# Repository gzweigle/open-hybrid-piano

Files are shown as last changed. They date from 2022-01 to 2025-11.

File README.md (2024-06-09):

# Hybrid MIDI Digital Piano

Also known as **stem piano**

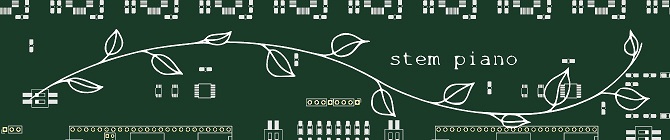
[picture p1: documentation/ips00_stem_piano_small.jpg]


## How to Build A Hybrid Piano
Go straight to the [pianos/](pianos/) directory!

But first, please read the [WARNINGS](WARNINGS.md) and [HELP](HELP.md) files that are located in this root directory.

See the [STATUS](STATUS.md) file for status of the project and repository.

If you would like to contribute hardware, software, mechanical, or firmware to the project, see the [CONTRIBUTING](CONTRIBUTING.md) file.

**If you build a piano, please share about it in the Show & Tell Discussions of this repository.**

## Overview

A hybrid piano combines the physical action of an acoustic piano with MIDI, sound generation, and other features of a digital keyboard. Some piano manufacturers sell hybrid pianos.

This project ("*stem piano*") is an open-source hybrid digital piano.

The qualifier digital is important. It means that signals are sampled with an analog-to-digital converter (ADC) and then all processing is with a microprocessor. Therefore, once the hardware is installed all algorithms, improvements, and new features are with software or firmware.

The repository includes schematics, printed circuit board layouts, firmware source files for the real-time processing, optional software source files for Ethernet connected features, and lists of required hardware components.

A physical piano action, or other instrument, is required. The electronics and code (*stem piano*) will work with a grand or upright piano action. Mechanical suggestions are included but not detailed mechanical instructions.

The platform and code could also adapt to building a range of other unique and innovative musical instruments.

## Directory Organization

The components required to build a piano are located in the [firmware/](firmware/), [hardware/](hardware/), [mechanical/](mechanical/) and [software/](software/) directories. In each directory is a *research* subdirectory and a *releases* subdirectory.

Each *research* subdirectory contains code and hardware for work in progress. It could have major bugs. It could be incomplete.

Each *releases* subdirectory contains code and hardware ready for use. The material in *releases* could partially duplicate material in one or more *research* subdirectories. However, the requirement is that anything in *releases* is well-tested, complete, and ready-to-use.

More details on each directory:

#### [design/](design/)

Designs and engineering analysis. To keep the repository small, associated data may be located in the separate Piano-Data repository.

#### [documentation/](documentation/)

High level documentation.

Includes [documentation/video_documentation.md](documentation/video_documentation.md) for historical, how-to, and other documentation in video form.

#### [pianos/](pianos/)

Building a complete piano requires firmware, hardware, mechanical, and sometimes software. The *pianos/* directory provides information on everything needed to build a specific version of a musical instrument.

Best place to start for learning the firmware, software, mechanical, and hardware.

#### [firmware/](firmware/)

Real-time code running on custom hardware from *hardware/* directory.

#### [hardware/](hardware/)

All printed circuit boards and related parts and design. A separate open-source license for the hardware is in this directory and applies to all hardware.

#### [mechanical/](mechanical/)

Anything to physically build a piano. A separate open-source license for mechanical is in this directory and applies to anything mechanical.

#### [software/](software/)

Code running on a standard computer or Raspberry Pi connected to the piano over Ethernet or MIDI.

## Repositories

#### (1) Original

This "DIY" repository. Organized per above.

#### (2) Stem Piano

https://github.com/stem-piano

Experimenting with a GitHub organization. The documentation and links for building individual pianos is here. Links are back to this original "DIY" repository.

May or may not migrate all files in the future. To be decided in the future.

## Related Projects:

Work was inspired, in part, by https://github.com/ekumanov/cybrid

See also:

* https://github.com/jkominek/piano-conversion/
* https://github.com/davidedelvento/Mybrid
* https://www.youtube.com/watch?v=nRBsudMpwwc
* https://www.youtube.com/watch?v=-kpf0OSJxkE
* https://www.youtube.com/watch?v=b-PRGymqECM

## "stem piano" because?

* science technology engineering math
* like a plant stem, everything here is one component of the overall instrument
* like a note stem, everything here is one component of...
* 12 leaves on the logo, matches 12 piano notes
* logo looks like a sine wave
* sounds cool
* does not sound cool

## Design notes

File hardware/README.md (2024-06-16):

# Stem Piano Hardware
See [kicad_general.md](./kicad_general.md) in this directory for information on the libraries.

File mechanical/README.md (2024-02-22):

# Mechanical Design

## Overview

The design is very flexible:
* Will work on grand and upright pianos.
* Will work with the action separate from the piano or as a silent system in a full piano.
* Will work with a digital keyboard, using sensors on the digital keys.
* Can use as part of innovative new musical instruments.

In the *documentation/* directory under the root directory is a file called video_documentation.md.  Please see for installation examples.

## Grand Piano - Separate Action Examples

### Stem Piano Model G

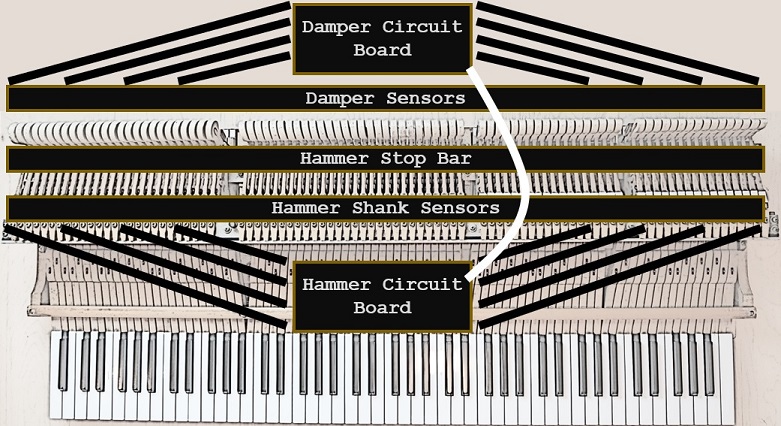
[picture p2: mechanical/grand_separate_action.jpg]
grand_separate_example


#### Damper Sensors

An aluminum L-shaped bar is placed across the back of the action. The damper sensors are mounted on this bar.

Connect the damper sensors to the circuit board that is processing the damper sensor output signals.

#### Hammer Stop Bar

Connect a strong steel bar that is anchored to something solid. Adjust height so that the hammer shanks hit this stop at the position where in a full piano the hammer would have hit a string.

#### Hammer Shank Sensors

An aluminum L-shaped bar is placed across the top-front of the action. The hammer sensors are mounted on this bar.

Connect the hammer sensors to the circuit board that is processing the hammer sensor output signals.

When two or more keys are pressed with identical force, the volume should be identical.  This note-to-note volume consistency is directly related to consistency of the sensor-to-shank physical distance between keys.

## Grand Piano - Silent System Examples

## Upright Piano - Separate Action Examples

## Upright Piano - Silent System Examples

## Innovative Instruments Examples

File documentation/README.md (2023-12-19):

# DIY Hybrid Digital Grand Piano - High Level Documentation

Three versions of the piano are in development. More are likely in the future. Further details, design, code, and hardware is in the root level *firmware*, *hardware*, *mechanical*, and *software* directories.

If a piano based on one of these architectures is stable enough for release, then information on all components required to build the piano is in the root level *pianos* directory.

## Performance Architecture
The original architecture.

Designed for maximum performance, without constraining cost or practicality. Sampling is fully parallel and in range 8Ksps to 32Ksps.

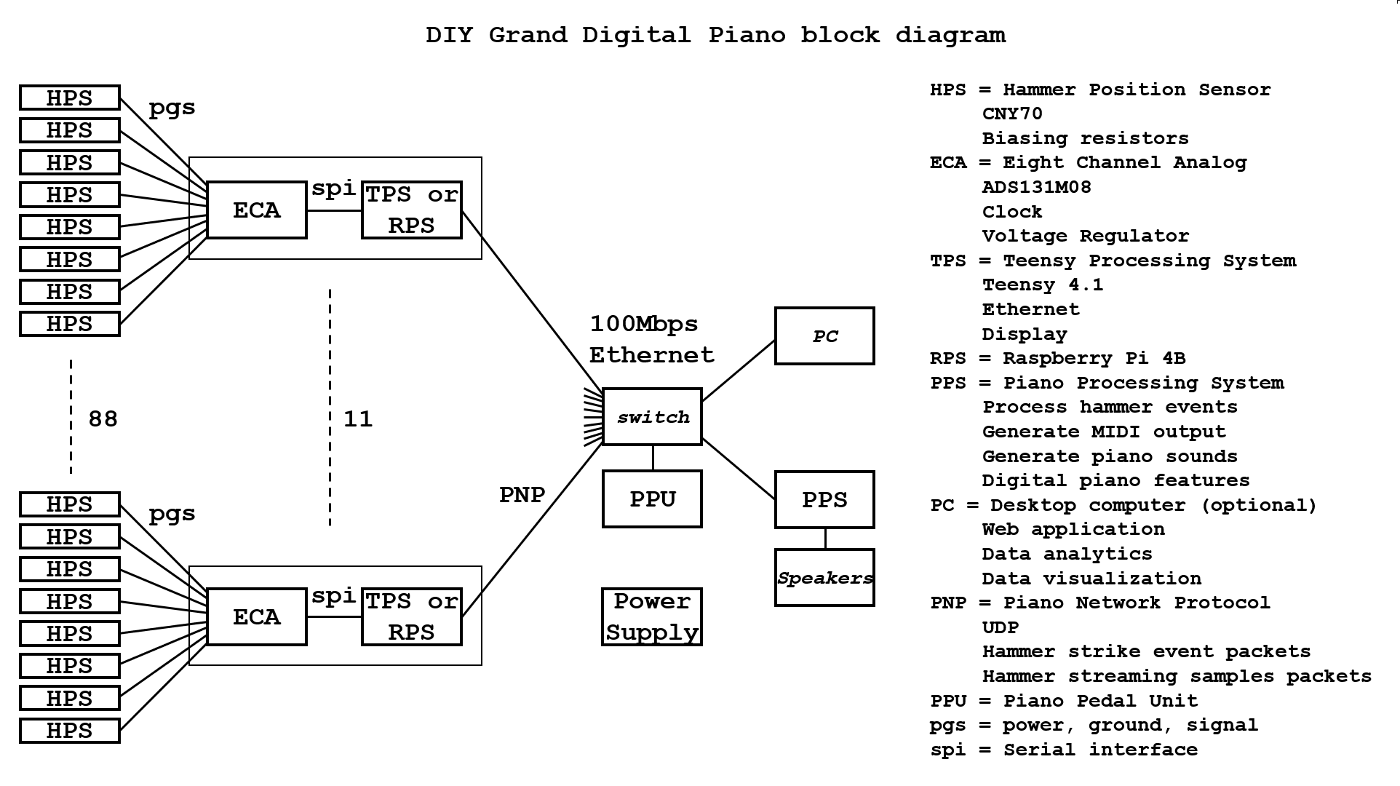
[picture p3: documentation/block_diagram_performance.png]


## Single Board Architecture 0.0
First single board architecture. An attempt to simplify and lower the cost. Sampling is fully parallel and in range 2Ksps to 8Ksps. Results show this architecture gives up performance without much benefit to simplicity or cost.

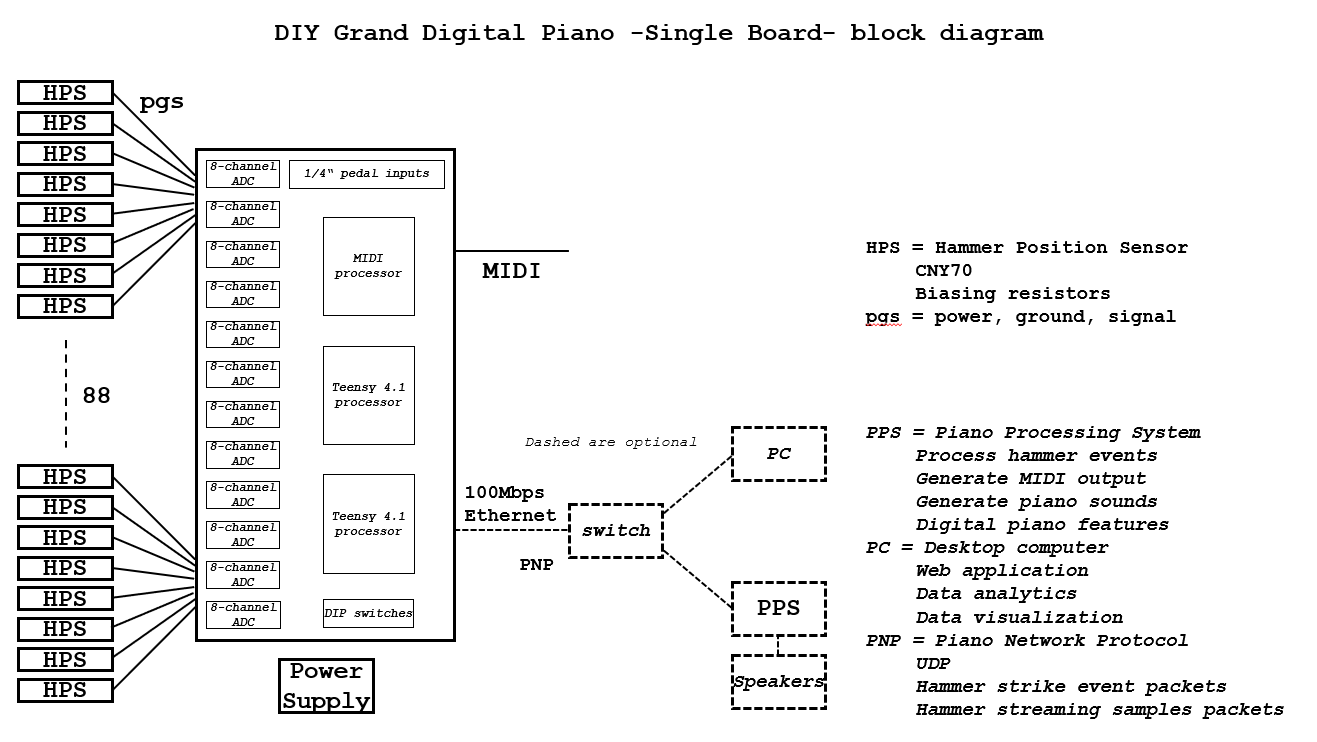
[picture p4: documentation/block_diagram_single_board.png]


## Single Board Architecture 2.0
Calling it "1.0" is too boring. Straight to 2.0!

Initially, this architecture was developed for damper processing. It was called the Damper Position Processor. Dampers do not need high-speed sampling and so, for dampers, sampling was fully sequential (a single ADC, multiplexed).

However, after testing and thinking more about it, I combined parallel plus sequential sampling into a design that scales from damper to hammer speeds. Preliminary analysis shows that the upper sampling limit could be close to the original performance architecture.

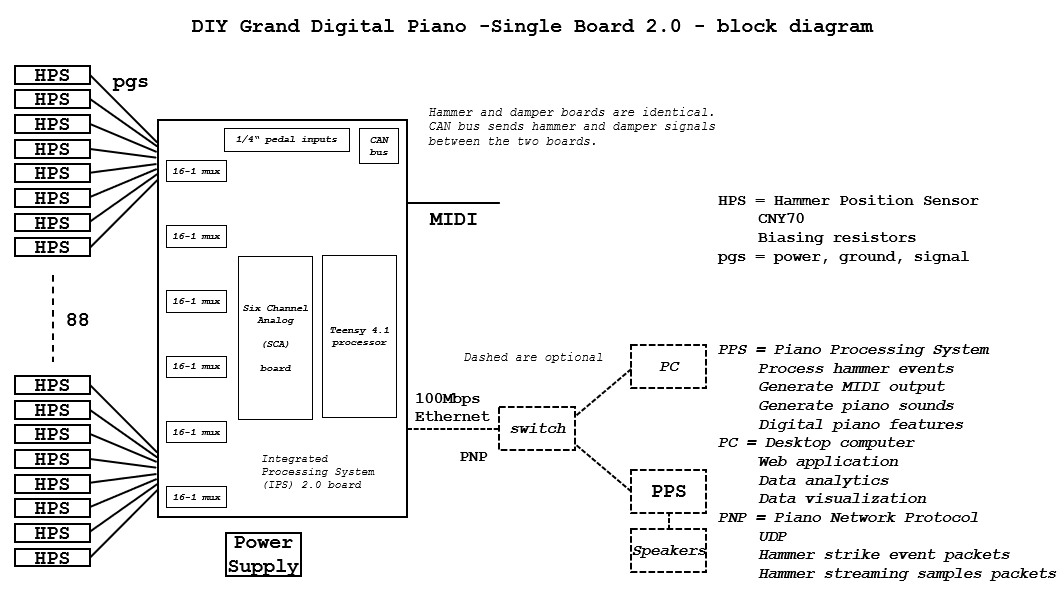
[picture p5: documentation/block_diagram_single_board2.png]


## Components Include:

Processors:
* Teensy 4.1 ARM Processor - https://www.pjrc.com/store/teensy41.html
* Raspberry Pi - https://www.raspberrypi.com/

Digital:
* Teensy to ADC interface logic ICs

Displays:
* Adafruit 2.8 inch TFT display - https://www.adafruit.com/product/1770

Analog:
* Texas Instruments ADS131M08 - https://www.ti.com/product/ADS131M08
* Texas Instruments ADS8861 - https://www.ti.com/product/ADS8861
* Texas Instruments ADS8860 - https://www.ti.com/product/ADS8860
* Texas Instruments ADCS7476 - https://www.ti.com/product/ADCS7476
* LTC6930 Precision Oscillator - https://www.analog.com/en/products/ltc6930.html
* 300mA - 500mA Low Dropout Linear Regulator
* 16:1, 8:1, and similar analog multiplexers
* CNY70 Sensor - https://www.vishay.com/en/product/83751/

Languages:
* Python - https://www.python.org/
* Matlab - https://www.mathworks.com/products/matlab.html
* C++

Printed Circuit Boards:
* OSH Park - https://oshpark.com/

## Video Documentation

Please see [YouTube Posts](video_documentation.md) for historical, how-to, and other documentation in video form.

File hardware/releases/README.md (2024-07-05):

# Hardware Releases

All released hardware is located in this directory.

See [../kicad_general.md](../kicad_general.md) for more information on KiCad files.

## Manufacturing

### Gerber Files

To manufacture a circuit board, send the files in a *_gerber/ folder to a PCB manufacturer. Board fabrication and test is always with the *_gerber/ folder files.

If the circuit board directory does not include a *_gerber/ folder, this means the boards have not been fully fabricated and tested. In this case, use the KiCad project. Once tested, add a *_gerber/ folder and files.

### KiCad Project Files

Boards for Gerber files were fabricated and tested.

Each directory of KiCad project files end with a "KiCad files" _v* version number. The KiCad libraries directories in this repository also end with the same "KiCad Files" _v* version number. Use the KiCad libraries directory with the same "KiCad files" _v* version number as the KiCad project files directories.

The "KiCad files" _v* version number system is a different numbering system than the KiCad program version and is different than the circuit board version. A unique "KiCad files" _v* version number for the KiCad directories allows flexible updates with anything related to KiCad changes.

### Components

Each bill of materials file ends with a number. This number allows different component variants for the same board. Piano building instructions will specify the bill of materials variant.

For any discrepancy between schematic and bill of materials, use the bill of materials. This includes part values as well as whether a through-hole component is placed on front or back of a circuit board.

## Numbering Systems Summary

* Circuit board version. Each circuit board version is in its own unique subdirectory.
* Bill of materials. The number on each bill of materials is for a board variant. Instructions for building each piano will specify the correct bill of materials variant.
* KiCad files _v* version number. Use this number to match KiCad files with the symbol and footprint library files in this repository.
* KiCad program version. If a circuit board directory includes multiple KiCad program versions, the circuit boards may have a silkscreen label indicating the KiCad program version used for fabrication.

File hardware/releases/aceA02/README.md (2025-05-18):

# Analog Condition Equalize (ACE) "A" - Version 0.2

Identical to ACE A 0.1 with the following changes:
* Add wire labels.
  * "+" = power
  * "-" = ground
  * "!" = signal
* Move connector labels closer to connectors.
* Space the resistors slightly further apart.
* Minor trace movement. No connectivity changes.

No functional changes.

See ACE A 0.0 for detailed description.

ACE A 0.0, 0.1, and 0.2 functionality and connectivity are identical.

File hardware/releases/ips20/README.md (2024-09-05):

# Integrated Processing System 2 (IPS2) specification

The mainboard for hammer or damper sensor connections and Teensy 4.1 processing.

## Features

### I/O
* The board supports 96 sensor inputs.
  * Either:
    * Analog interfaces to 88 hammer sensor boards, or
    * Analog interfaces to 88 damper sensor boards.
  * 3 pedal inputs: 1/4 inch.
  * With less pedal inputs, it is also possible to use extra inputs for more than 88 piano keys.
  * With less piano key inputs, it is also possible to have more pedal inputs.
* MIDI output.
* Ethernet interface (optional).
* +5 volt, 1.75 amp power input. Current is when using with 88 HPS 0.4 or HPS 0.8 sensors. Current input could be different with alternate sensor.
* CAN bus.

### Capabilities
* Process hammer samples and generate MIDI outputs.
* Process damper samples and send to hammer processing board.
* Process pedal samples and generate MIDI outputs.
* Dual in-line package switches for configuration.
* Optional advanced monitoring, setup, and analytics over Ethernet and web brower.
* Optional hammer and pedal data over Ethernet using the piano network protocol (PNP).
* Optional TFT display for setup.

### Components
* Selected for availability.
* Relatively large pitch, relatively easy to solder parts.
* Requires a Six Channel Analog (SCA) card.
* The parts list(s) includes an index number in the file name to support differences depending on application. Files:
  * [./ips20_bill_of_materials_0.txt](./ips20_bill_of_materials_0.txt)

## Form
* 8.5 inches by 4.0 inches.
* Single board.

## Top Level PCB Description

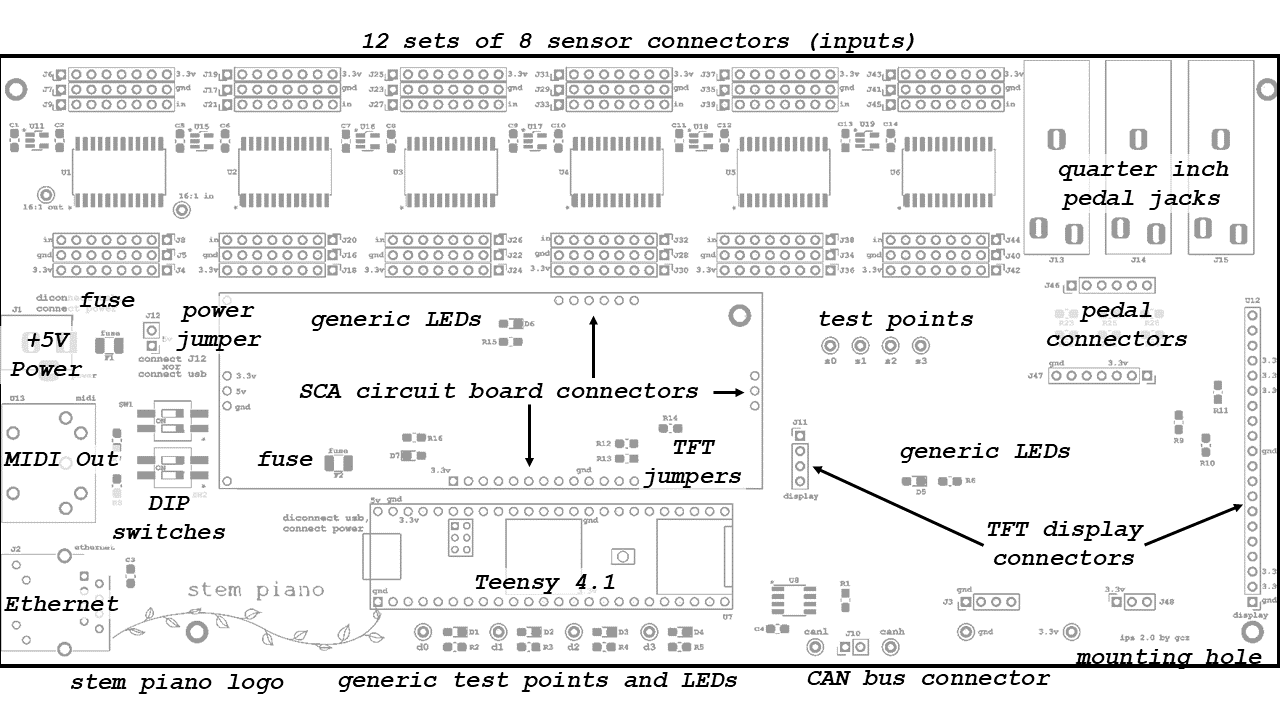
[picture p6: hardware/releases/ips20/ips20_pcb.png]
ips20_pcb


### Sensor connectors
0.1 inch spaced connectors for connecting wires to the Hammer Position Sensor (HPS) boards. Does not require HPS boards. Can connect to any sensor system that meets input signal requirements.

### Quarter inch pedal jacks
For connecting pedals.

See discussion in issue: https://github.com/gzweigle/DIY-Grand-Digital-Piano/issues/74

### Pedal connectors
0.1 inch spaced connectors J46. Connect to six of the sensor connectors. See instructions in the *pianos/* directory for this board.

### +5V power

* Cut the 5V pad on Teensy 4.1 per instructions at PJRC website before installing the Teensy processor. https://www.pjrc.com/teensy/external_power.html

* See: https://github.com/stem-piano/stem-piano-top/blob/main/WARNINGS.md

### Fuse

Location for fuses. The +5V power and USB must must automatically protect from short circuits, overcurrent, thermal, and all other failure conditions

User to decide on PCB fuse design and strategy. See the bill of materials file(s) in this directory.

Here is a short video on the *stem piano* historical progress YouTube channel about removing and replacing a surface mount fuse. Also see other resources on the internet.
https://www.youtube.com/watch?v=TsNTWSIT84I

### Power jumper (J12)
Install only after 5V pad on Teensy 4.1 is cut per instructions at PJRC website.

https://www.pjrc.com/teensy/external_power.html

### MIDI Out
Five-pin MIDI output connection. The board does not have a MIDI input.

### Ethernet
Ethernet connection.

### DIP switches
For simple configuration settings. Programmable with the Teensy firmware. See code for functionality.

### SCA circuit board connectors
The analog-to-digital conversion (ADC) subsystem is on a separate, removable, card that connects to the IPS printed circuit board. This simplifies and reduces the cost of testing an ADC and enables experimenting with different hammer or damper ADC resolution and sampling rates. Also, ADC parts can often be in packages that are difficult to solder. A separate circuit board lowers the cost and impact of soldering mistakes.

Headers J3, J47, and J48 make it possible to increase the size of the SCA. This allows larger and more complex analog circuits. In this case, either do not use the TFT, or use longer connectors so the TFT is above the SCA.

### Generic test points and LEDs
Programmable test points and LEDs through the Teensy firmware.

### Teensy 4.1
What makes everything possible.

### TFT jumpers
Zero-ohm resistors R12, R13, and R14. Only needed if TFT display is connected.

### CAN bus connector
Connect two wires between hammer and damper circuit boards. If not using a damper circuit board then leave these disconnected. Connect each wire to the same location on the other board (left side of connection to left side, right side to right side).

### TFT display connectors
Connection for optional 2.8-inch display.

### stem piano logo
Yeah!!

## Power Supplies and Connections

[ips20_power.md](./ips20_power.md)

## Design
Location of timing analysis: [../../../design/data_acquisition/eca0X_ips2X/eca0X_ips2X_timing_design.md](../../../design/data_acquisition/eca0X_ips2X/eca0X_ips2X_timing_design.md).

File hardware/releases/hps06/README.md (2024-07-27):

# Hammer Position Sensor (HPS) Version 0.6

## Introduction

Originally, the HPS PCB was for hammers.  However, the sensor also works for dampers.  Not changing the name because many circuit boards have already been built.

This circuit board includes a trimming resistor. Unless needed for a specific use case, the circuit board with trimming resistor is not recommended.

In repository for historical reasons.

## Features

### I/O
* Power input.
* Analog output signal, with range set by resistors.
* Ground.

### Size
* 1.5 inches long.
* 0.4 inches wide.

### Capabilities
* CNY70 sensor.
* Trimming resistor to fine tune output voltage maximum value.
* All resistors are surface mount packages.

### Pin Order:
* Power
* Signal
* Ground

## Calibrating

Adjust the RV0 trimming resistor to get the output voltage in the correct range. A 1.0mm flathead screwdriver is required. Turn the screw slowly and gently. Information according to the datasheet [Bourns 3224 - 4mm SMD Trimpot Trimming Potentiometer, C1753 5/17/18]:
* Adjustment angle = 12 turns.
* Rotational cycling max = 200 cycles.

Based on testing, typical adjustment is no more than approximately 2 turns clockwise or counterclockwise. This results in a resistance range of approximately 75 to 125 ohms.

Turning the RV0 trimming screw clockwise decreases the resistance between pins 2 and 3 of the trimming resistor RV0 ==> this decreases the combined resistance R1 + RV0 ==> this increases the forward current of the CNY-70 emitter ==> this increases the output voltage.

Turning the RV0 trimming screw counterclockwise increases the resistance between pins 2 and 3 of the trimming resistor RV0 ==> this increases the combined resistance R1 + RV0 ==> this decreases the forward current of the CNY-70 emitter ==> this decreases the output voltage.

R2 sets the maximum output voltage. If the output voltage is too large, the analog-to-digital converter will clip. If the output voltage is smaller, it decreases the dynamic range. The piano will work with a lower dynamic range but may not work if the signal is clipping. Therefore, if the R2 value in bill of materials is unavailable, choose a smaller value.

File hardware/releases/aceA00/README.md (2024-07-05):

# Analog Condition Equalize (ACE) "A" - Version 0.0

## Introduction

The ace A is an interposer card between sensors and mainboard for analog signal translation.

Each ace A snaps onto the mainboard at 16 sensor connections at rear of mainboard.

Each interposer function is identified by a letter.

| Letter | Function |
|---|---|
| A | Resistor load (this README file)  |
| B | Transimpedance amplifier (future) |
| Z | Pass through (future) |

## Description

Each ace card connects 16 sensors to the mainboard. See the specific stem piano construction documentation for connection details.

Circuit diagram.
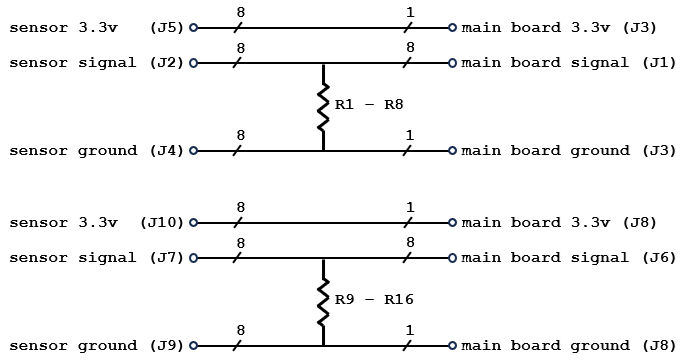
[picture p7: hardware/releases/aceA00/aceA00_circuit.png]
aceA00_circuit


Top and bottom side of ace A.

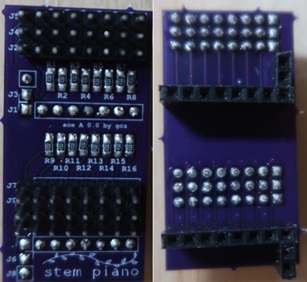
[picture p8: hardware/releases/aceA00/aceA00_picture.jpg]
aceA00_picture


## I/O

Note - Unlike the stem piano mainboards, the ace A boards do not have "input", "3.3v", and "ground" labels. Refer to the associated mainboard for double checking connections.

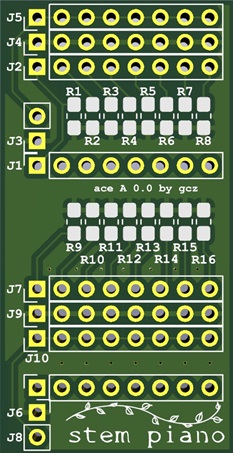
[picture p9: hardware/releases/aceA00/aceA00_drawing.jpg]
aceA00_drawing


### Connections to mainboard.

These socket connectors are on the bottom side of ace A.

Note - J6 label is next to J8. It should be next to the adjacent eight pin connector footprint that is 0.1 inches above J8.

| Connector | Function |
| --- | --- |
| J1 | Connects to 8 mainboard sensor input pins. |
| J6 | Connects to 8 mainboard sensor input pins. |
| J3 pin 2  | Pin near J1. Connects to mainboard ground. |
| J3 pin 1  | Connects to mainboard 3.3v output. |
| J8 pin 2  | Pin near J6. Connects to mainboard ground. |
| J8 pin 1  | Connects to mainboard 3.3v output. |

### Connections to the sensors.

These pin connectors are on the top side of ace A.

| Connector | Function |
| --- | --- |
| J2 | Connects to 8 sensor outputs. |
| J7 | Connects to 8 sensor outputs. |
| J4 | Connects to 8 sensor grounds. |
| J9 | Connects to 8 sensor grounds. |
| J5 | Connects to 8 sensor 3.3v inputs. |
| J10 | Connects to 8 sensor 3.3v inputs. |

### Size
* 1.84 inches by 0.95 inches.
* Single board.

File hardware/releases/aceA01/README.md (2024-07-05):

# Analog Condition Equalize (ACE) "A" - Version 0.1

Identical to ACE A 0.0 with the following changes:
* Removed ground plane because it makes soldering more difficult (thermal) and adds little benefit.
* For headers placed on back of board, corrected the footprints to match.
* Adjusted some of the footprint label locations.

No functional changes.

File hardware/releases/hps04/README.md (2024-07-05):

# Hammer Position Sensor (HPS) Version 0.4

## Introduction

Originally, the HPS PCB was for hammers.  However, the sensor also works for dampers.  Not changing the name because many circuit boards have already been built.

## Features

### I/O
* Power input.
* Analog output signal, with range set by resistors.
* Ground.

### Size
* 1.5 inches long.
* 0.4 inches wide.

### Capabilities
* CNY70 sensor.
* Fixed resistors.
* All resistors are through hole.

### Pin Order:
* Power
* Signal
* Ground

## Resistors

R2 sets the maximum output voltage. If the output voltage is too large, the analog-to-digital converter will clip. If the output voltage is smaller, it decreases the dynamic range. The piano works with a lower dynamic range but may not work if the signal is clipping. Therefore, if the R2 value in bill of materials is unavailable, choose a smaller value. If the R1 value is unavailable, choose a larger value.

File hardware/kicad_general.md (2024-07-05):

# KiCad General Information

KiCad information and also information about the KiCad libraries located in this directory.

## Libraries

### Versions
Library directories are versioned in case future KiCad changes force library changes.
* kicad_libraries_v0 - Version 0. Works with files for KiCad 7.
* kicad_libraries_v1 - Version 1. Works with files for KiCad 8.

### Use 

Should be possible to load a KiCad project, view the schematic, view the PCB, and send files for fabrication without loading the *stem piano* specific symbol and footprint libraries.

To add the *stem piano* symbol and footprint libraries in this directory, see the KiCad documentation for symbol and footprint library management.

* Use the Nickname *stem_piano_footprints* in KiCad when loading the footprint libraries.
* Use the Nickname *stem_piano_symbols* in KiCad when loading the symbol libraries.

### KiCad 7 Contents

* Project-specific symbols file. Use with schematic editor. [kicad_libraries_v0/stem_piano_symbols.kicad_sym](kicad_libraries_v0/stem_piano_symbols.kicad_sym)
* Directory of project-specific footprints for the printed circuit board (PCB) layout: [kicad_libraries_v0/stem_piano_footprints.pretty/](kicad_libraries_v0/stem_piano_footprints.pretty/).

### KiCad 8 Contents

* Project-specific symbols file. Use with schematic editor. [kicad_libraries_v1/stem_piano_symbols.kicad_sym](kicad_libraries_v1/stem_piano_symbols.kicad_sym)
* Directory of project-specific footprints for the printed circuit board (PCB) layout: [kicad_libraries_v1/stem_piano_footprints.pretty/](kicad_libraries_v1/stem_piano_footprints.pretty/).

## Design Rule Checking

Schematic design rule check possible warnings and errors:
*	**Error**: power pin not driven. Why does this happen? Some symbols do not match the power type on pins. For example, using a header to jumper power. Could fix (future) by creating specific symbols for these cases or adding PWR_FLAG. As long as know why the error happens for each case, it is ok.
* **Error**: no simulation model. Why does this happen? Upgrading between KiCad versions. Select ignore SPICE model issue in the Electrical Rules settings.
* **Warning**: symbol has been modified in library. Why does this happen? Upgrading between KiCad versions.

PCB design rule check possible warnings and errors:
*	**Warning**: Silkscreen clipped by board edge. This is cosmetic.
*	**Warning**: Silkscreen overlap. This is cosmetic.
*	**Warning**: Footprint does not match library. Why does this happen? Could be due to KiCad updates. To eliminate warnings, in the PCB Editor may need to select a footprint and then run the update. However, this could reorient the silkscreen text.
*	**Error**: Thermal relief connection to zone incomplete. Why does this happen? Too few ground connections make soldering more difficult because of heat transfer. In some locations tight spacings made it difficult to get extra ground connections. Is not a problem for hand solder but could cause problems for automated soldering. Check with manufacturer.
*	**Error**: Courtyards overlap. Why does this happen? Usually a close spaced header or test point. Is not a problem for hander solder but could cause problems for automated soldering. Check with manufacturer. If it is a problem, could solve be changing to a combined part. For example, instead of three 1x8 headers, use a single 3x8 header.

The most important error to watch for is unconnected items or schematic parity. This happens if the schematic and PCB do not match. In some cases, these errors are because of KiCad updates. Either fix the error or visually verify (caution!) correctness of schematic vs PCB.

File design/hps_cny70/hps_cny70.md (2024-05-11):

# Analog Front-End for HPS, using CNY70

This directory contains information on the analog front-end design for *stem piano* using the Hammer Position Sensor (HPS) boards with CNY70 sensors.

Selecting the HPS resistors and getting an output voltage in the correct range could involve some trial-and-error testing when building a *stem piano*. The reason is because of many influences on the output voltage:
* Reflective surface.
* Variation between CNY70 parts.
* Physical distance between hammer shank and the CNY70.

This document explains the reasons behind resistor values in the bill of materials for the HPS boards. Understanding the design and resistor selection process is helpful because each piano is unique and could require adjustments.

The project progress YouTube videos https://www.youtube.com/@gzpiano88 may prove helpful and links are provided below.

## HPS Block Diagram

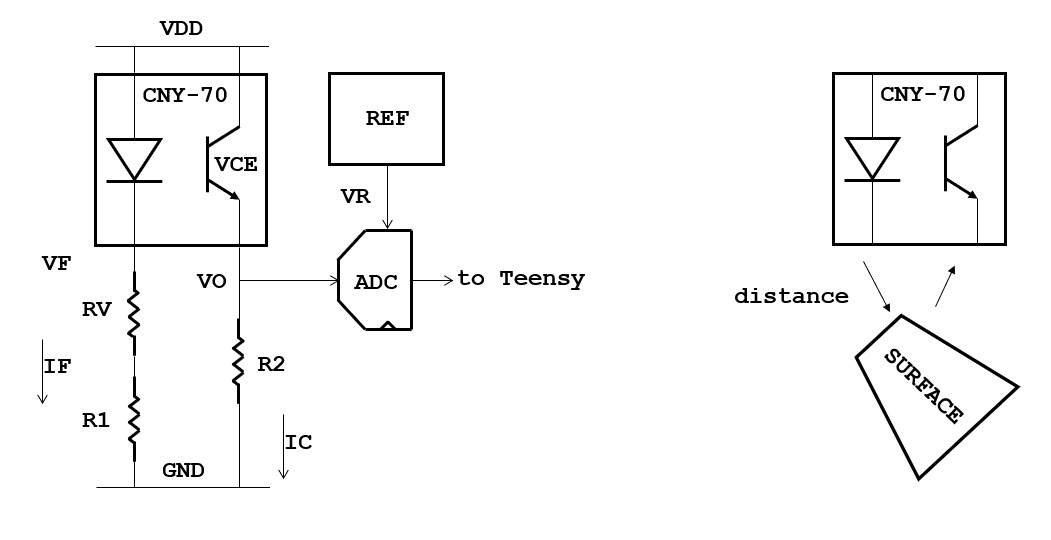
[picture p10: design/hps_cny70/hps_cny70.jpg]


The R1, R2, and RV values are in the HPS bill of materials. Also in the bill of materials is the REF integrated circuit component (unless integrated with the ADC). The information below explains how values are selected. Additional resources are the CNY70 data sheet [1] and application guide [2]. See end of this file for the full names of those documents.

Resistor RV is optional and in most cases is not needed.

## Definitions

### HPS Components
* CNY70 = Optical sensor.
* ADC = Analog to Digital Converter.
* REF = Something generating the ADC reference voltage. This is an external integrated circuit or it is included with the ADC.
* SURFACE = Reflective surface such as a hammer shank or the damper location at back of a piano key.
* R1 = Resistor to set forward current IF.
* RV = Optional adjustable resistor to put CNY70 output close to full ADC dynamic range. See this video for an explanation of the CNY70 variation issue: https://www.youtube.com/watch?v=C9174TC4kLs
* R2 = Resistor to set the value of VO when CNY70 distance is closest to the SURFACE.

### Electrical Quantities
* VDD = Power supply voltage.
* GND = Ground.
* VO = Output voltage of the sensor board, with respect to GND.
* VF = Emitter voltage, with respect to GND.
* VR = Reference voltage, with respect to GND.
* VCE = Voltage across the receiver. Measure as VDD - VO.
* IF = Forward current of light emitter.
* IC = Collector current at light receiver.

### Physical Quantities

* *distance* = vertical distance from the CNY70 to a reflective surface.

## Design Constraints

* VO must always be within the input range of the ADC.
    * VO > 0
    * VO < VR 

* VF is set by the CNY70. See CNY70 data sheet [1]. A typical value is 1.2V.

* VR is selected during design. Primary considerations on the value VR include keeping VCE in proper range when VO is at its largest value and using the maximum ADC dynamic range over all values of VO.

* VCE must be within the constant current range specified by CNY70 data sheet figure 6 [1]. Typical ranges:
    * VCE > 0.4V
    * VCE < 10V (individual designs may be less)

* Forward current IF. The upper range limit listed here is smaller than the datasheet because the *stem piano* design takes into account worst-case temperature [2] restrictions.
    * IF > 5mA
    * IF < 25mA (absolute max, individual designs may require less)

* For collector current IC, see CNY70 data sheet [1] figure 9 for an example of IC vs *distance*.

## Design Principles

### Use the Full Range for VO

The ADC receive a voltage VO from the HPS sensor board, and then the ADC outputs an integer value to the Teensy microprocessor. The Teensy microprocessor normalizes that integer value into a floating-point value in range [0, ..., 1]. When VO = 0, the floating-point value is 0.  When VO = VR, the floating-point value is 1. When VO = *X* * VR, the floating-point value is *X*, where 0 < *X* < 1.

* When the *distance* is at its largest value (hammer shank is at rest), VO is close to zero, and the Teensy value is close to 0.
* When the *distance* is at its smallest value (hammer shank is hitting the hammer stop bar), VO = VR, and the Teensy value is 1.

The algorithms in the Teensy are designed for values in the full range [0, ..., 1]. If less than the full range are used, it could cause problems for the algorithms.

Often the smallest value is larger than 0. For example, 0.2. This is ok. However, if the largest value is larger than 1 or too much smaller than 1, this can cause problems.

The range of VO depends on R1, R2, and the *SURFACE* reflectivity.
* A smaller (R1+RV) or larger R2 results in a larger VO.
* A larger (R1+RV) or smaller R2 results in a smaller VO.
* A more reflective *SURFACE* results in a larger VO.
* A less reflective *SURFACE* results in a smaller VO.

### Examples of VO Not Full Range

#### R1 too large or R2 too small or *SURFACE* not reflective enough
Consider a scenario where the voltage output VO = VR/2 when the hammer shank is hitting the hammer stop bar, instead of at the expected value of VO = VR. Then the Teensy computes a value of 0.5. In this case, if an internal algorithm is expecting something closer to 1.0 (for example 0.8), the Teensy might not infer that the hammer hit the stop bar. And, the Teensy might not output a MIDI event, even though the hammer did hit the hammer stop bar.

#### R1 too small or R2 too large or *SURFACE* too reflective
Consider if VO = 1.1 * VR when the hammer shank is hitting the hammer stop bar. Then the ADC clips the signal, because the signal exceeded VR. In this case, because of clipping, the Teensy gets a value of 1.0 instead of 1.1. This causes problems for the Teensy algorithms.

#### Problems for VO and hammer at rest
As another example, consider a scenario of VO = VR/2, instead of VO closer to zero when the hammer is at rest. In this case the Teensy may think that a key is being held down, and may not release the sustain MIDI signal.

### Selecting the Correct values of R1, RV, R2, and *SURFACE* reflectivity

The resistor values in the HPS bill of materials were selected by engineering analysis and then by testing many CNY70. The resistor values attempt to ensure VO < VR for all variants of CNY70. This means that for some CNY70, the output voltage VO is much less than VR.

Unfortunately, each CNY70 exhibits a slightly different response for the same values of R1, RV, and R2. Some CNY70 output larger VO and some CNY70 output smaller VO. The following subsections describe solutions if VO is too small or too large on for some CNY70.

#### VO Too Small

* Correct by firmware calibration in the Teensy. Measure the output and multiply by a constant to increase the floating-point value.
* Correct by using a version of HPS with VR, and adjust VR smaller to increase VO until VO = VR when the *distance* is at its smallest value. See [../../hardware/releases/hps07/README.md](../../hardware/releases/hps07/README.md) for directions on adjusting VR.
* Test many CNY70 and throw away the ones with small output voltages when in the HPS circuit configuration.
* Use a more reflective surface. When selecting R1, RV, R2 in the bill of materials, the system was tested with a white sheet of printer paper. White printer paper has one of the highest reflective surfaces according to [2]. When the circuit boards are installed on the piano, if the *SURFACE* is the piano shank wood, it will have a lower reflectivity. Then VO is lower. If VO is too low (for example, the piano does not play at all or plays poorly), put white stickers on each piano shank or damper.  See *stem piano* video https://www.youtube.com/watch?v=ZMxMio3L9dk at approximately 0:45 time mark for an example. Another option is white paint.
* Position the sensor rail closer vertically to the hammer or damper.

#### VO Too Large

*IMPORTANT* - In general, it is better to select R2 too small than too large (similarly it is better for too large R1 than too small). While a value of R2 too small makes VO too small and that could cause problems described above, these problems are fixable with firmware.

However, if R2 is too large (similarly R1 too small), the output voltage VO clips. The firmware cannot fix clipping because the signal is distorted. If the signal clips, fix it in hardware either by:

* Correct by using a version of HPS with VR, and adjust VR later to decrease VO until VO = VR when the *distance* is at its smallest value. See [../../hardware/releases/hps07/README.md](../../hardware/releases/hps07/README.md) for directions on adjusting VR.
* Test many CNY70 and throw away the ones with VO > VR when in the HPS circuit configuration.
* Using a less reflective surface, such as adding a sticker or paint with less reflectivity.
* Position the sensor rail further away vertically from the hammer or damper.

To avoid clipping, the goal of resistor values in the HPS bill of materials is that when the hammer is hitting the hammer stop bar, the output voltage VO is slightly less than VR.

### Circuit Testing

Before assembling a *stem piano*, it is recommended to test each HPS board to check that VO < VR when the CNY70 is very close to *SURFACE* and in the *stem piano* HPS circuit configuration.

See these *stem piano* videos for examples of process:
* https://www.youtube.com/watch?v=uJTaKLZaluc at approximately the 2:20 time mark.
* https://www.youtube.com/watch?v=w0TpXvcRCsM at approximately the 1:15 time mark. The target output voltage in the video is for a first generation architecture. Other architectures use other maximum voltage values. Check instructions for each piano to find the correct maximum output voltage for that piano.

Options:

* Assemble the entire *stem piano*. Manually move each piano shank up and down between rest position and contacting the hammer stop bar. Visually observe the internal Teensy float value by one of the following methods:
    * Best option: edit the firmware so the Arduino serial monitor displays the Teensy internal float value for each key, one at a time.
    * Alternate: write software on a computer that receives Ethernet values from the *stem piano* and displays the results on a computer.
    * Alternate: install the TFT display on the circuit board. Select a switch to enable the display (if this is the option in the version of *stem piano* built). The display shows the internal Teensy float value.
* Build a small prototype breadboard test station. Connect a power supply and ground to the power and ground HPS pins. Connect the HPS output voltage to a multimeter or oscilloscope. Move a piece of white paper close to the CNY70 sensor. Measure the output voltage and check that it is in proper range.

## Other Considerations

According to [2], a smaller value of R2 results in a larger bandwidth. R2 = 2000 ohms is approximately 10KHz bandwidth. Tests show R2 < 5000 ohms work ok.

The CNY70 output voltage degrades with time [2]. Expect 10% loss at 1,000 hours and 20% loss at 10,000 hours. However, at normal room temperature the lifetime is longer [2]. If after many years the piano does not play as well, check the voltage VO of each CNY70 with a multimeter or oscilloscope.

Room lighting and ambient lighting could interfere with the CNY70 operation [2].

The output voltage VO could drop suddenly if the *distance* between CNY70 and *SURFACE* gets very close to zero. When building the sensor rail and piano frame, position each CNY70 so that when the hammer shank or damper is at the closest *distance* to the CNY70, there is at least a 0.5 millimeter *distance* between the CNY70 and the hammer or damper. As this gap gets larger, the maximum VO decreases. So, the *distance* gap cannot be too large.

The piano note volume consistency is sensitive to the consistency of the CNY70 and hammer shank gap between keys.

## References

These documents are on the Vishay website.

[1] *"Reflective Optical Sensor with Transistor Output"*, CNY70, Vishay Semiconductors, Rev. 1.8, 30-Jul-12.

[2] *"Application of Optical Sensors"*, Rev. 1.0, 27-Sept-06.

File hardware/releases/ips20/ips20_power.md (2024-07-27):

# Integrated Processing System 2 (IPS2) power

All external power supplies must automatically protect from short circuits, overcurrent, thermal, and all other failure conditions. See https://github.com/stem-piano/stem-piano-top/blob/main/WARNINGS.md.

## Diagram

The IPS circuit board is powered through the "+5V power" input at middle left of IPS circuit board.

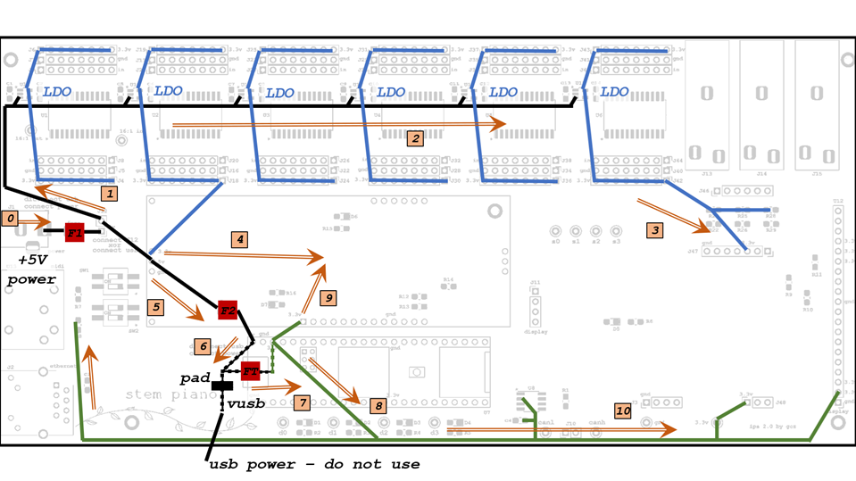
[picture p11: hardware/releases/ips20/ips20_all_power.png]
ips20_all_power


## Pad

Cut the 5V pad (labeled "pad" on diagram above) on Teensy 4.1 processing PCB per instructions at PJRC website before installing the Teensy 4.1 processing PCB. https://www.pjrc.com/teensy/external_power.html

## Diagram Description

Items: (line routing in diagram is similar to but not exactly as traces on PCB):
* Black = +5 volt lines.
* Blue = +3.3 volt lines for analog power.
* Green = +3.3 volt lines for digital power.
* Red = Fuses F1, F2, and FT.
* Orange = Current flow.

Voltage converters not shown. A change in line color indicates voltage level conversion.

Solid lines are on IPS PCB.

Lines with dash are on the Teensy 4.1 processing PCB. Please refer to the PJRC website for latest Teensy 4.1 schematic and documentation. https://www.pjrc.com.

* Fuse FT. This is a 500mA PTC type fuse. On Teensy schematic it is labeled F1. Rename FT here to avoid confusion with IPS circuit board fuse F1.
* "pad": must cut before installing Teensy 4.1 processing PCB to block receiving +5 volts and current from USB.

## Power Supplies and Connections

### +5 Volt Input

Tests show the IPS circuit board normally draws almost 1.5 amps. See *stem piano* video at the approximate 2:20 time https://youtu.be/TemXGmkoc-g?t=140.

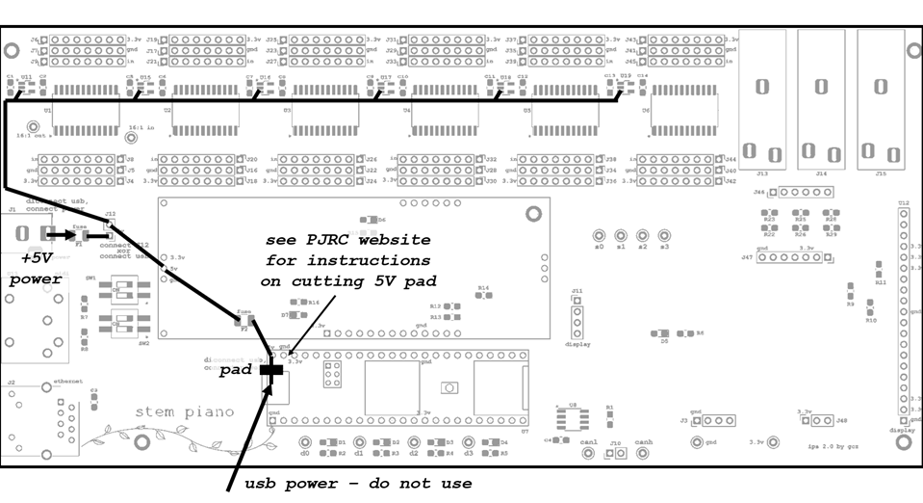
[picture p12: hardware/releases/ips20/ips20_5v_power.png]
ips20_5v_pcb


### +3.3 Volt Analog

See blue lines in figure below.

Six Low Dropout (LDO) voltage regulators. Each converts +5 volts to +3.3 volts. Each LDO powers a single 16:1 analog multiplexer plus 16 remote sensors. One also connects to the pedal circuit and one also connects to the SCA.

Current of each:
* 16 HPS 0.8.  Current is 16 * 11 mA = 176 mA.
* 16:1 multiplexer. According to its data sheet, the 16:1 analog mux worst-case current draw is 16mA (use twice the (ICC + delta ICC) values).
* The pedal circuit draws approximately 5 mA.
* The SCA current draw depends on the SCA circuit. Seems unlikely this would exceed 50mA.

Current summation:
* Four LDO connect only to HPS and a multiplexer.  Current = 4 * (176 mA + 16 mA) = 768 mA.
* One connects to HPS, a multiplexer, and the SCA.  Current = 176 mA + 16 mA + 50 mA = 242 mA.
* One connects to HPS, a multiplexer, and the pedal resistors.  Current = 176 mA + 16 mA + 5 mA = 197 mA.

Total current = 1207 mA

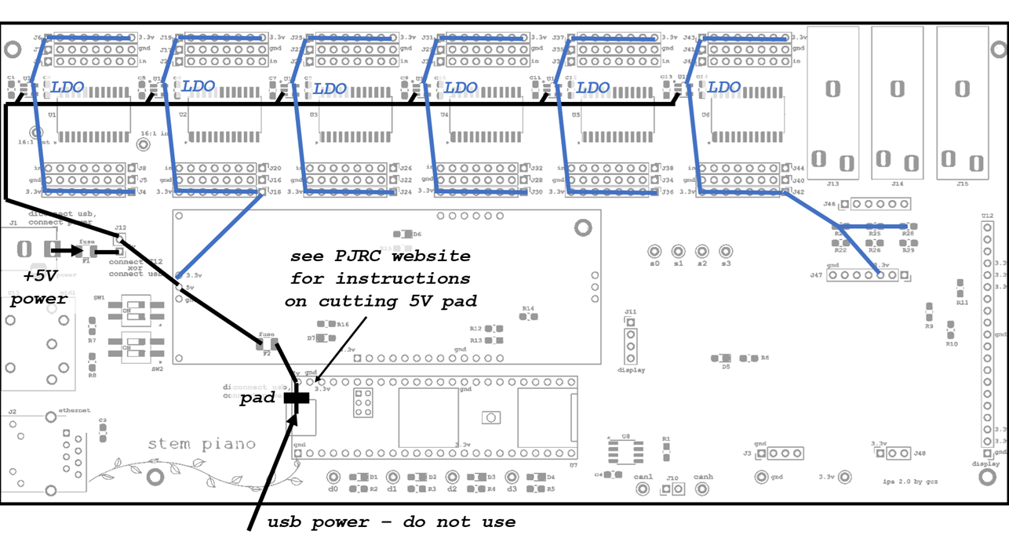
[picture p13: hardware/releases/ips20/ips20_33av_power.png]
ips20_33av_pcb


### +3.3 Volt Digital

See green lines in figure below.

The Teensy 4.1 includes a 3.3 volt output (green).

This output connects to the SCA, the Can bus, the TFT display, the MIDI connector, and one of the optional SCA headers (J48). When designing an SCA board that uses the +3.3 volt digital input, the current draw of TFT display and Can bus must be considered.

Current of each:
* According to the display datasheet, the TFT display (far right connector) takes 80 mA.
* According to the Can bus datasheet, the Can bus integrated circuit (middle bottom) takes less than 60 mA normally but can take as much as 180 mA during a bus fault. Using Can bus is optional.

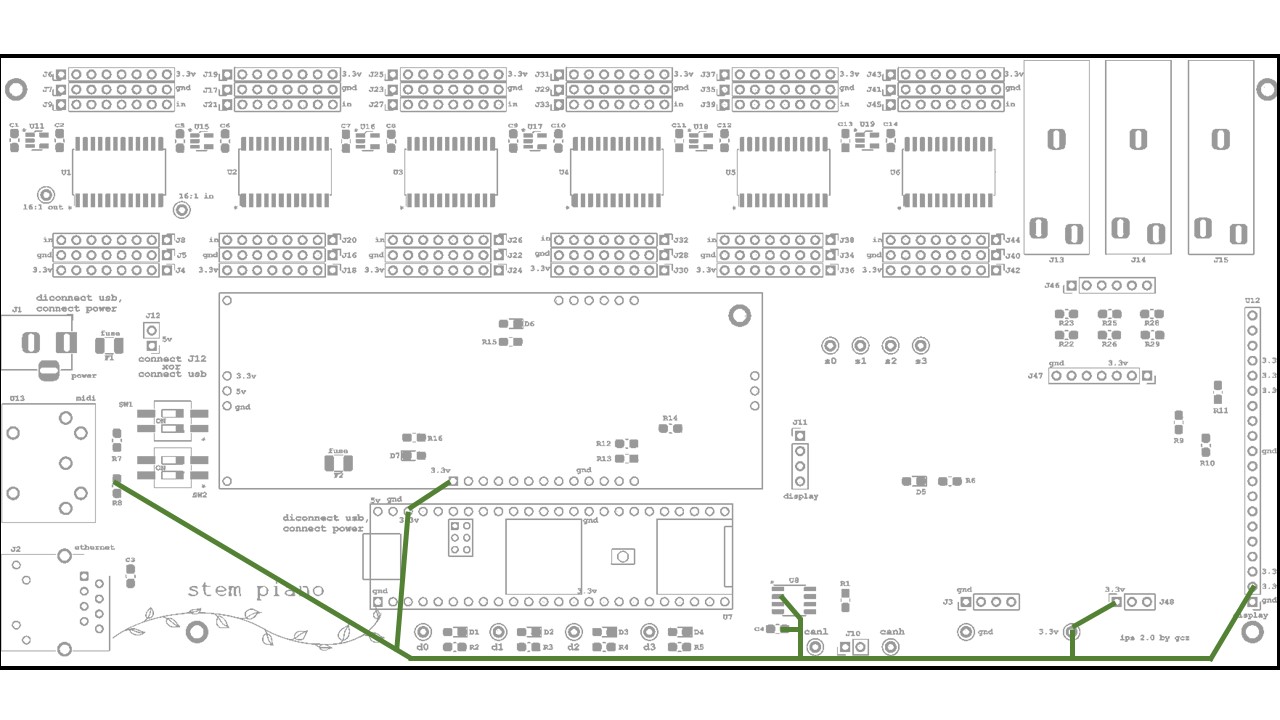
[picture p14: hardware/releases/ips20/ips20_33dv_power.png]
ips20_33dv_pcb


## Power With USB Input

Not in design scope.

Considerations:

If "pad" is not cut then do not use the "+5V power" input.

Current flow (5) and (6) reverse direction and current flow (0) is zero amps.

Not installed:
* J1 barrel jack.
* Fuse F1.
* J12 jumper.

Change F2.

USB has an enumeration process that determines current. The IPS circuit board may not support. See USB standard. The USB power source must meet the same requirements as the "+5V power" source.

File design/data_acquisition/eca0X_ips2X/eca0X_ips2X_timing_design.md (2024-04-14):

# Timing Diagrams for ECA 0.X / IPS 2.X

Design is for:
* Firmware: *six_channel_analog_00.cpp* located here: [../../../firmware/releases/StemPianoIPS2/](../../../firmware/releases/StemPianoIPS2/)
* Hardware: [../../../hardware/releases/sca00](../../../hardware/releases/sca00)
* Hardware: [../../../hardware/releases/ips20](../../../hardware/releases/ips20)

Pianos:
* Stem Piano G: [../../../pianos/StemPianoG/](../../../pianos/StemPianoG/)

Timing requirements are from [1], [2], and [3].

All timing values below were verified with an oscilloscope.

## Top Level Timings (No Damper Board Option)

* *t_rate* = Overall sample rate. Set by the variable *adc_sample_period_microseconds* in the file *hammer_settings.cpp* located here: [../../../firmware/releases/ips2_hammer/](../../../firmware/releases/ips2_hammer/).
* *t_stem* = Total time for all piano processing. With a damper board this time increases because of the CAN bus processing time.
* *t_margin* = Extra margin. Set *t_rate* so that *t_margin* is large enough to accommodate interrupts, processing variability (if/else paths), and any other statistical cases. Larger is safer. Smaller increases the overall sample rate.
* *t_acq* = Total acquisition time for all 96 analog channels. The value 1.520 is from the diagram in the **Data Acquisition** section of this document.
* *t_proc* = Total processing time for all firmware running on the Teensy, except data acquisition. Examples:
    * Hammer, damper, and pedal processing
    * Ethernet
    * MIDI
    * CAN bus (if using a separate damper processing board)
    * Switches, test points, LEDs
    * Run-time calibration
    * TFT display
    * Overhead code and miscellaneous tasks

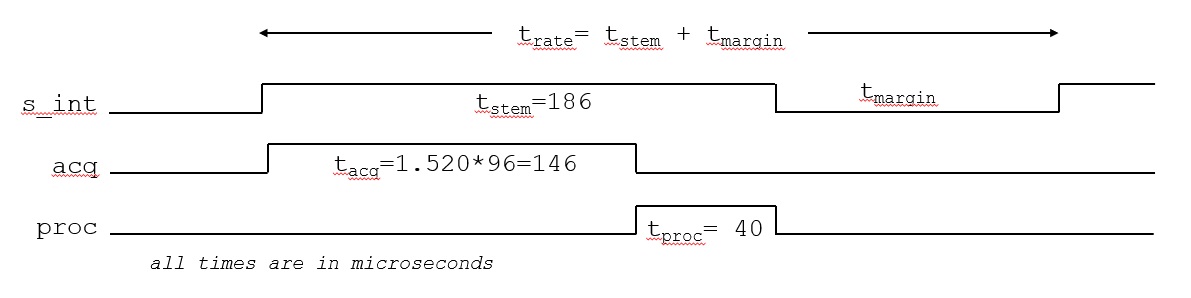
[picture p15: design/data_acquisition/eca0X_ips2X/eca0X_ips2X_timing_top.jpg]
timing_top


## Data Acquisition

The data acquisition is pipelined. An analog input value is sampled by the ADC at first *convst* rising edge (A) and the conversion result is sent to Teensy on SPI *sclk* shown. The firmware switches the PCB multiplexers to input analog value (B) immediately after *convst* rising edge. Switching early increases total settling time margin. The new analog input value (B) is sampled at second *convst* rising edge.

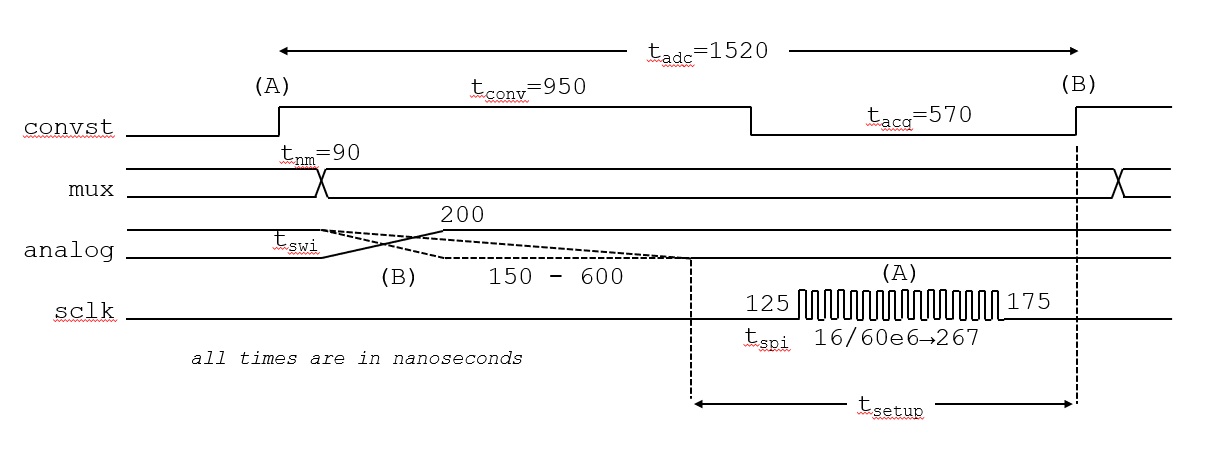
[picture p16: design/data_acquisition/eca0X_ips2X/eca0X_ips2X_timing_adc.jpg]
timing_acq


* *t_adc* = Processing time for a single input. Must be larger than 1000 nanoseconds [1][2][3].
* *t_conv* = Time to convert a single channel. Must be larger than 710 nanoseconds [1][2][3].
* *t_acq* = Time to acquire a channel. Must be larger than 290 nanoseconds [1][2][3].
* *t_nm* = Time for Teensy to calculate mux values for next channel.
* *t_swi* = Time for analog settling after 16:1 and 8:1 muxes switch. Must completely settle prior to *t_setup*. The minimum *t_setup* value is 290 nanoseconds [1][2][3]. From the diagram, measured *t_setup* is over 800 nanoseconds. So, the design has good settling time margin.
* *t_spi* = SPI timings. Example shown is for a 60 MHz SPI clock frequency.

## How To Speed Things Up?

To sample piano hammers and dampers faster, the following are possible. After making changes, must validate that the *t_stem* + *t_margin* are not longer than the processing interval timing code in *src_hammer.cpp*. Verify using an oscilloscope.

Options:

* Decrease *t_conv* closer to the 710 nanosecond minimum. The present design uses a timer which is very conservative, but guaranteed. To go faster, change firmware to rely on processing timings. After *t_conv* is smaller, then decrease *adc_sample_period_microseconds* accordingly in the settings file.

* Speed up SPI clock. The max rate is 70MHz. The present design is 60MHz to give extra timing margin. After changing the clock frequency, decrease *adc_sample_period_microseconds* accordingly in the settings file.

* Decrease *t_margin*. Do this by decreasing *adc_sample_period_microseconds* directly in the settings files.

* Optimize Teensy processing firmware to decrease *t_proc*. After *t_proc* is smaller, then decrease *adc_sample_period_microseconds* accordingly in the settings file.

* Add more ADC in parallel by designing a new SCA board! Increment the SCA major version number (for example, call it SCA 1.0). Must not require changing the more expensive IPS board.

## References

[1] "ADS8860: 16-bit, 1-MSPS, serial interface, single-ended input, SAR analog-to-digital converter", Texas Instruments, February 2019.

[2] "ADS8861: 16-bit, 1-MSPS, serial interface, true-differential input, SAR analog-to-digital converter", Texas Instruments, December 2013.

[3] "ADS8881: 18-bit, 1-MSPS, serial interface, true-differential input, SAR analog-to-digital converter", Texas Instruments, August 2015.

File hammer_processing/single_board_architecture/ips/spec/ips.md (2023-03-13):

# Integrated Processing System (IPS) specification

## Requirements

### I/O
* Analog interfaces to 88 HPS boards.
* 3 pedal inputs: 1/4 inch.
* MIDI output.
* Ethernet interface (optional).
* 5 volt, 2.5 amp power input.

### Capabilities
* Process hammer samples and generate MIDI outputs.
* Process pedal samples and generate MIDI outputs.
* LED indicators of hammer height for visual check of proper hammer to sensor distances.
* Dual in-line package switches for configuration.
* Optional advanced monitoring, setup, and analytics over Ethernet and web brower.
* Optional hammer and pedal data over Ethernet using the piano network protocol (PNP).

## Form
* Single board.
* Low profile.

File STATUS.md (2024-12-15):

# Hybrid MIDI Digital Piano - Status and Milestones

## Status

The Stem Piano G hardware and firmware in the repository works and is a very playable piano.

Depending on pianist skill, the piano accuracy may need further improvement. For example, the action frame and sensor mechanical system tolerances cause note-to-note dynamics variation. Also, sensor errors have been improved but are not zero.

## Major Historical Milestones

### November 29, 2024 - First Independent Build

A second open-hybrid-piano / stem-piano has been independently built and is working.

### April 21, 2024 - Accuracy Improvement

Improve note-to-note consistency. Eliminate trimming resistors.

### November 26, 2023 - Open Source Hybrid Piano, Digital Architecture

Finished pushing all files to the repository.

### November 10, 2023 - Finish Stem Piano G

First time a full 88 key piano with the simpler architecture is functional.

### March 16, 2023 - First 88 Key Piano

First time my full 88 key piano is functional, including pedals. Built from a mix of two architectures.

### March 7, 2023 - Single Board Architecture

First piano subset for the single board architecture.

### January 15, 2023 - Pedals

First working with three pedals.

### July 8, 2022 - High Performance Architecture

First piano subset with the high performance architecture.

### January 2, 2022 - Started Open Source

Created repository.

### July 24, 2021 - Eight Piano Keys

My first working piano with more than one note.

### June 11, 2021 - First Datapath

Full datapath is functional, one note.

### December 27, 2020 - Project Kickoff Video

First YouTube video. Quality was poor. Remake video January 1, 2022.

### December 5, 2020 - Start Project

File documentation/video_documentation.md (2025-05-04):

# Hybrid MIDI Digital Grand Piano - Video Documentation

Some videos may no longer be posted or the URL may have changed.

Step 1 - Architecture https://www.youtube.com/watch?v=P3PVIuGSpIk

1. High-performance digital architecture approach.
2. Selecting the (Arduino) Teensy 4.1 processor.
2. Testing the CNY70 sensor, temporarily using the (Arduino) Teensy internal ADC.
3. Building a single-key action for testing.
4. Writing C++ software on the (Arduino) Teensy and Python on my computer to get something working for the first time.
5. Testing.

Step 2 - Analog Subsystem https://www.youtube.com/watch?v=p1Ko1ZMaAus

(audio was accidentally recorded mono channel)

1. Selecting the Ti ADS131M08 32Ksps 24-bit 8-channel analog-to-digital converter (ADC).
2. Learning the ADC.
3. Building a test system by modifying a Ti Evaluation Module.
4. Connecting the ADC to the (Arduino) Teensy via SPI.
5. Writing ADC SPI driver C++ software on the (Arduino) Teensy.
6. Testing.

Step 3 - Digital Signal Processing https://www.youtube.com/watch?v=5eaIhX29dF4

(audio was accidentally recorded mono channel)

1. Designing an algorithm that converts ADC samples of the hammer position into key strike events and velocities.
2. Implement the algorithm in C++ software on the (Arduino) Teensy.
3. Testing the algorithm with the single-key action and ADC subsystem.

Step 4 - Piano Action Frame https://www.youtube.com/watch?v=5U7LvOMth28

(audio was accidentally recorded mono channel)

1. Designing the physical layout of future PCB boards with respect to a grand piano action.
2. Designing the layout of circuit boards for the analog subsystem and microprocessors.
3. Building a wood frame for a piano action that includes hammer stops and sensor mounts.

Step 5 - Printed Circuit Boards https://www.youtube.com/watch?v=6EG-CYtTOFs

(audio was accidentally recorded mono channel)

1. Partitioning the design into two circuit boards.
2. Hammer Position Sensor (HPS 0.0) PCB: CNY70, biasing resistors, connection to microprocessor.
3. Hammer ENcoder (HEN 0.0) PCB: ADS131M08, power supply, (Arduino) Teensy 4.1.
4. Circuit design for both boards.
5. PCB layout for both boards.
6. Fabrication at OSH Park.
7. Software modifications to support new system.

Step 6 - Learning to Solder https://www.youtube.com/watch?v=wlrAXrDVhN0  (removed)

(audio was accidentally recorded mono channel)

1. After receiving the circuit boards, I had difficulty hand soldering small surface mount parts.
2. So, I took time to learn the science of soldering.

Step 7 - HPS PCB (CNY70) https://www.youtube.com/watch?v=usbgk9fsZ5I (removed)

(audio was accidentally recorded mono channel)

1. Finalize selection of biasing resistors.
2. Document design process for selecting biasing resistors.
3. Solder CNY70 and resistors on the board.
4. Testing.

Step 8 - HEN PCB https://www.youtube.com/watch?v=tCwKCgKxA0A

1. Design new (HEN 1.0) circuit board to add a clock and change physical orientation.
2. Circuit design and layout.
3. Soldering parts on the new HEN printed circuit board.
4. Continue C++ software development for the (Arduino) Teensy.
5. Bringing up the board and testing.
6. Full system test with HPS 0.0 and HEN 1.0
8. Write Python software on my computer to generate MIDI signals for sound generation through an external digital keyboard.

Step 9 - Raspberry Pi 4B https://www.youtube.com/watch?v=q-dFU-f_Ju8

1. Investigate the possibility of using a Raspberry Pi 4B in place of the (Arduino) Teensy 4.1.
2. Modify the (Arduino) Teensy C++ software to include a lower layer that abstracts the hardware.
3. Test with Ti Evaluation Module from Step 2.
4. Get system running.
5. Investigate but do not solve challenges with obtaining sufficiently fast real-time performance from Linux.
6. Although I made no physical changes to the Pi, for reference I am calling this the Raspberry Processing System (RPS).

Step 10 - Testing with Piano Action https://www.youtube.com/watch?v=ANJI4KAolEw

1. Layout three new HPS variations: HPS 0.1 changed the header spacing, HPS 0.2 increased the length slightly to get better alignment over the hammer shanks, HPS 0.2D is with the After Dark OSH Park fabrication process.
2. Investigate slight changes to bias resistors. Based on discoveries when tested with piano action.
3. Connect 8 Hammer Position Sensor (HPS, various versions) boards to 1 Hammer ENcoder (HEN 1.0) board.
4. Mount on the frame from Step 4 and place on a physical grand piano action.
5. Precisely locate each hammer stop position to exactly match hammer position when action is in the piano.
6. Continue improving the (Arduino) Teensy (HSP) C++ software and computer Python software.
7. Test.

Step 11 - Latency https://www.youtube.com/watch?v=k5ro7su6gYo

1. Investigate a problem with latency discovered during Step 10.
2. Quickly learn this was due to very large Ethernet packets containing hammer samples for visualization.
3. Remove that software (it was temporary for testing).
4. Measure the system latency.

Step 12 - Board Split https://www.youtube.com/watch?v=3AoEzj19FGQ

1. During the course of this project I am learning that soldering is very time consuming.
2. Want to avoid soldering 88 HPS boards and 11 HEN boards, then needing a board spin.
3. Decide to split the HEN into two boards.
4. New Board #1: (Arduino) Teensy Processing System (TPS) - contains the (Arduino) Teensy, Ethernet, and a new LCD (marginally useful features!).
5. New Board #2: Eight Channel Analog (ECA) - contains the Ti ADS131M08, associated support circuitry, and connections to the HPS.
6. Advantage of the split: TPS is easy to solder and likely to change. ECA is difficult to solder and unlikely to change.
7. Design and layout of TPS 0.0.
8. Soldering and bringing up the TPS.
9. Testing the TPS, discover a problem with the LCD write times.
10. Design a solution to long LCD write times.
11. Changes to (Arduino) Teensy C++ software to work around the write time issue.

Step 13 - Eight Channel Analog https://www.youtube.com/watch?v=e2ARDHr45-I
1. Soldering and bringing up the ECA (version 0.0).
2. Testing the ECA with the TPS and associated (Arduino) Teensy 4.1
3. Testing the ECA with a Raspberry Pi 4B (named the RPS).

Step 14 - Network and PPS https://www.youtube.com/watch?v=ryVUUPXWy0Q

1. Design a network protocol for sending hammer strike events (basically, MIDI information) and high-speed streaming hammer samples (for data analysis and visualization).
2. Design the protocol such that it avoids the latency issues seen in Step 11.
3. Writing protocol C++ software for TPS/RPS.
4. Writing Python for the Piano Processing System (PPS) portion of the design.
5. The PPS is running on another Raspberry Pi 4B and is responsible for converting hammer strike events into piano sounds, the MIDI interface, and other similar features.  The PPS is intended to implement features found on a modern digital keyboard.
6. Presently the PPS only generates MIDI. Other features are for the future.
7. Writing Python and Matlab / Octave software for my desktop computer to receive streaming samples, store them in a temporary cache, and plot the data in real-time. This is all temporary software for testing.
8. Redo the ECA layout so it works better with a Raspberry Pi 4B.
9. Use ECA 0.0 with TPS 0.0 and ECA 0.1 with RPS.
10. Testing.

Step 15 - Dedicated Piano Action https://www.youtube.com/watch?v=xohaQG593e4

1. Kawai KG-3C action with damper rail.
2. New sensor rail.

Step 16 - Thin Film Transistor LCD https://www.youtube.com/watch?v=y42pQxGMDy0

1. Design a different LCD approach, that avoids the timing issues discovered in Step 12.
2. Research LCD options and select the following: 2.8", 240x320 pixel, color, with capacitive touch.
3. For performance add a second processor for graphics processing.
4. Research processor options - select the Teensy 4.1 for graphics processing.
5. Write software for graphics display with Teensy 4.1.

Step 17 - TPS Mechanical https://www.youtube.com/watch?v=PopMsf95C8o (removed)

1. Design a physical case set that meets these requirements:
   1. Fits an ECA board, two Teensy 4.1 processing systems, ethernet/power connectors, and the TFT LCD.
   2. Accommodates all wiring - HPS (sensors), ethernet, power, and debugger connections.
   3. Fits within width of piano action.
   4. Meets thermal requirements.
   5. Looks cool.
2. Build cardboard and PCB mock-ups to test various ideas.

Step 18 - Two Teensy PCB https://www.youtube.com/watch?v=M1_228-ClXM

1. Design and write the software for DSP Teensy - GPU Teensy communication.
2. Breadboard test the DSP Teensy and GPU Teensy communication software (and connections).
3. Layout a new TPS (0.1) with DSP and GPU Teensy, that works with ECA 0.1, and fits the physical case.
4. Test new TPS.
5. Mechanical: ECA connection, case modifications, and external power supply.
6. Modifications to PPS Python software to support new features.
7. Full system running with eight piano keys, new boards, and lots of software changes.

Step 19 - Sixteen Key Piano https://www.youtube.com/watch?v=oMMNmDyscmQ

1. HPS 0.3 - Shorten board and build soldering jigs to reduce construction tolerances.
2. ECA 0.2 - Shorten so fits better in previously designed case, add ECA/TPS mounting holes, 0.1" alignment to aid soldering.
3. TPS 0.2 - Modifications for case fit, 0.1" alignment, add missing LED resistors.
4. Shorten LCD side-mounting PCB so fits better in case.  Add 2 LED.

Step 20 - Sensor Improvement https://www.youtube.com/watch?v=C9174TC4kLs

1. HPS 0.4 - Remove top ground plane. Not needed and looks better with the dark PCB option.
2. Investigate uneven hammer max height signal - discover cause is CNY70 variations.
3. Could address either with firmware calibration or external trimmer resistor.
4. Design and build HPS 0.5 with a trimmer resistor. This gives ability to test both options.
5. HPS 0.5 also switches to surface mount resistors to give space for the trimmer.

Step 21 - Twentyfour Key Piano https://www.youtube.com/watch?v=uJTaKLZaluc

1. ECA 0.3 - Larger pads for voltage regulator.
2. TPS 0.3 - Move LCD forward to give additional TFT to ECA clearance. Add card detect pull-up resistor.
3. Build one additional ECA/TPS to achieve a total of 24 keys.
4. Build 24 of the new HPS 0.5.
5. Adjust HPS 0.5 trimmers to get a flat hammer max height signal.

Step 22 - 40 Keys, 3 Pedals https://www.youtube.com/watch?v=9sqkgVXceJU

1. Design and build a voltage divider circuit with three pedal inputs.
2. Design algorithms (not covered in video) to estimate pedal resistance from voltage divider output.
3. Use an existing ECA/TPS 0.3 for processing voltage divider output.
4. Write new C++ for Teensy pedal processing and Teensy pedal TFT display.
5. Modify PPS Python to support pedals.
6. Build 16 of a new HPS 0.6 design (will be covered in future video).
7. ECA 0.4 - Small changes to help soldering.
8. TPS 0.4 - Move a couple LEDs to make more visible.
9. TPS goes back to original TFT position, and I built new vertical stand PCB to fine-tune position.
10. Build three new ECA/TPS.

Step 23 - Single Board Architecture https://www.youtube.com/watch?v=DxdRO3M7cgg

1. Introducing the single board architecture.
2. Why?
3. Board design.
4. Initial testing: Teensy-ADC logic and new C++ software.
5. The new board is called Integrated Processing System, or IPS.  Video covers IPS 0.0.

Step 24 - 88-Key Piano Build https://www.youtube.com/watch?v=w0TpXvcRCsM

1. While attempting to play subsets of Mozart K331 Andante grazioso:
2. Build updated version of all 88 sensors (HPS circuit boards).
3. Solder 6 of 12 analog-to-digital converters, plus associated circuitry, on IPS 0.0.
4. Test and correct bugs in software for multiple sets of analog-to-digital converters.
5. Test and correct an issue with printed circuit board.
6. Finally - a working 88-key custom hybrid digital piano!

Step 25 - MIDI: PCB and Software Problems https://www.youtube.com/watch?v=gNeLMGaxmG0

1. Solder a single new ADC plus pedal circuit and MIDI circuit onto the board used for Step 23 and Step 24.
2. The new ADC is connected to the pedal circuit.
3. The new ADC is also connected to the second (Treble) Teensy.
4. This setup enables testing code for full ADC data synchronization and using both Teensy processors.
5. This setup also enables testing the custom Teensy2Teensy communication link.
6. Modify PCB to connect only a single clock (LTC6930 Precision Oscillator) to all ADC.
7. Modify PCB to merge ADC resynchronization lines into a single line, controlled by the Base Teensy.
8. Test triple pedal works.
9. Stress test MIDI and debug.
10. Stress test MIDI and debug.
11. Stress test MIDI and debug.

Step 26 - Damper Velocity https://www.youtube.com/watch?v=ZMxMio3L9dk
1. Damper sensor mechanical.
2. Damper sensor PCB, called Damper Position Processor (DPP).
3. Testing DPP.
4. Reusing the Hammer Position Sensor (HPS) for DPP. Since using sensor for both hammer and damper, will need to rename.
5. CAN Bus for sending data between DPP and hammer board (either IPS or TPS).
6. Adding display to DPP.

Step 27 - Hammer and Damper Processing https://www.youtube.com/watch?v=NmziaIYKS1g
1. Extend board for dampers (last video) to support hammers and dampers.
2. Fully multiplexed architecture.
3. Testing various analog designs.
4. All 88 keys are working with the new architecture.
5. For the dampers, some use direct sensors and some are estimated based on hammer position.
6. Testing boards and code.
7. This is the hardware and firmware of the initial Stem Piano Model G release - [Stem Piano Model G](../pianos/StemPianoG/)

Step 28 - Precision and Accuracy https://www.youtube.com/watch?v=TemXGmkoc-g
1. Analyze position and velocity for (attempting to) strike 10 notes simultaneously.
2. Build system that could be used for a future CNY-70 sensor calibration system.

Step 29 - Fixing Sources of Inaccuracy https://www.youtube.com/watch?v=yqkRKSGX6kw
1. Analyze and fix mechanisms causing note-to-note inconsistency:
2. Piano action.
3. Horizontal sensor position.
4. Vertical sensor position.
5. CNY70 - nonlinearity.
6. CNY70 - out of tolerance.
7. Crosstalk.
8. Shank angle.
9. Analog front end.
10. Reflective material.
11. Ambient light.

Step 30 - Testing boards from a new manufacturer https://www.youtube.com/watch?v=tyN7v7L9VIQ
1. Manufacture boards directly from GitHub artifacts (https://github.com/gzweigle/open-hybrid-piano/tree/main/hardware/releases) and with a new manufacturer.
2. This tests everthing was correctly pushed to GitHub.
3. Construct a piano based on GitHub instructions (https://github.com/stem-piano) and GitHub firmware (https://github.com/gzweigle/open-hybrid-piano/tree/main/firmware/releases).
4. This tests that all the GitHub material is correct.

Step 31 - Web application displaying all 96 streaming measurements https://www.youtube.com/watch?v=AWMlzoCq9G0
1. Write a python server that receives streamed hammer position measurements from the piano.
2. Write a javascript program that displays values from all 96 sensors in real time.
3. Write and play a song to go with it.
4. This tests the full Ethernet datapath.

Step 32 - Another video displaying streaming measurements https://www.youtube.com/watch?v=jlyA7hVRj5U
1. Modify the python server.
2. Write a javascript program with another display idea.
3. Write and play a song to go with it.

Step 33 - Upgrading hammer sensors https://www.youtube.com/watch?v=QIp7ZoWRtdo
1. Switching to the low-cost sensors (HPS 0.8) and verify that the GitHub HW works. 
2. Test a set of approximately 400 CNY-70 and sort by peak voltage.
3. Select 88 CNY-70 with peak voltage in range 2.2 volts to 2.5 volts.
4. Use r2 = 4300 ohms.
5. Build 88 sensors based on HPS 0.8.
6. Build 6 ACE boards based on ACE 0.0 and 0.1.
7. Replace old hammer sensor HPS with the new HPS.
8. Test.

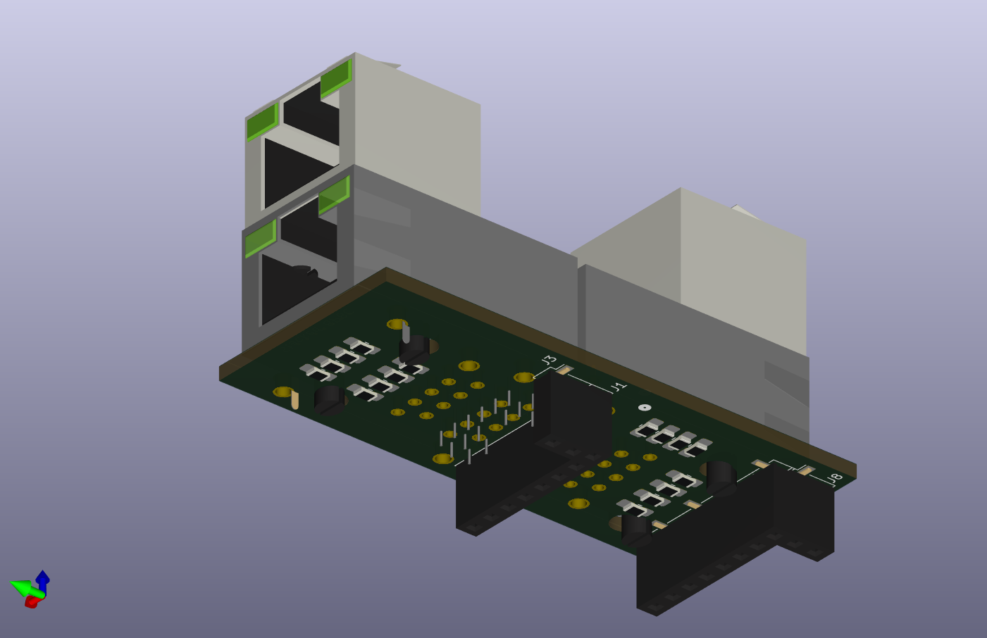
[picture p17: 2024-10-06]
hardware/research/aceA01-eth/aceA01-eth/aceA01-eth.png

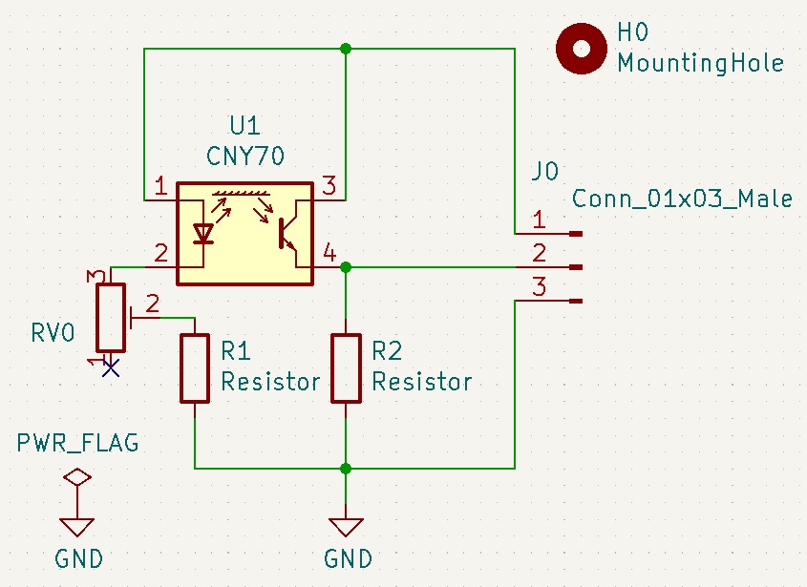
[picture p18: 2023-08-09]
hardware/releases/hps06/hps06_schematic.jpg

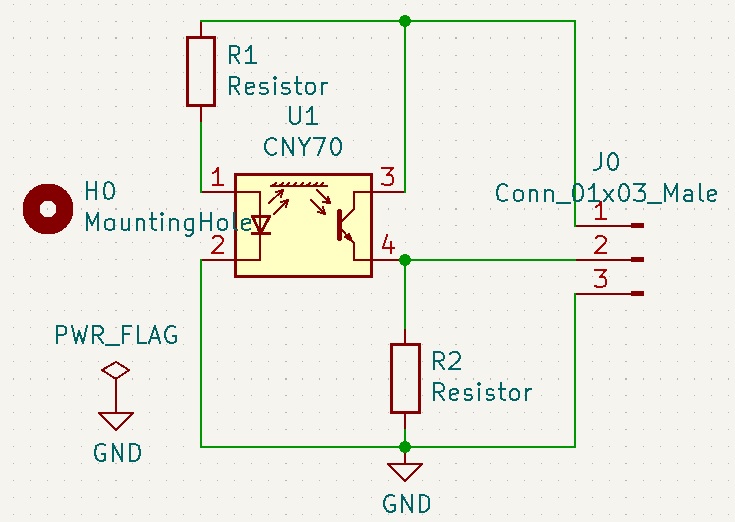
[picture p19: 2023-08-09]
hardware/releases/hps04/hps04_schematic.jpg

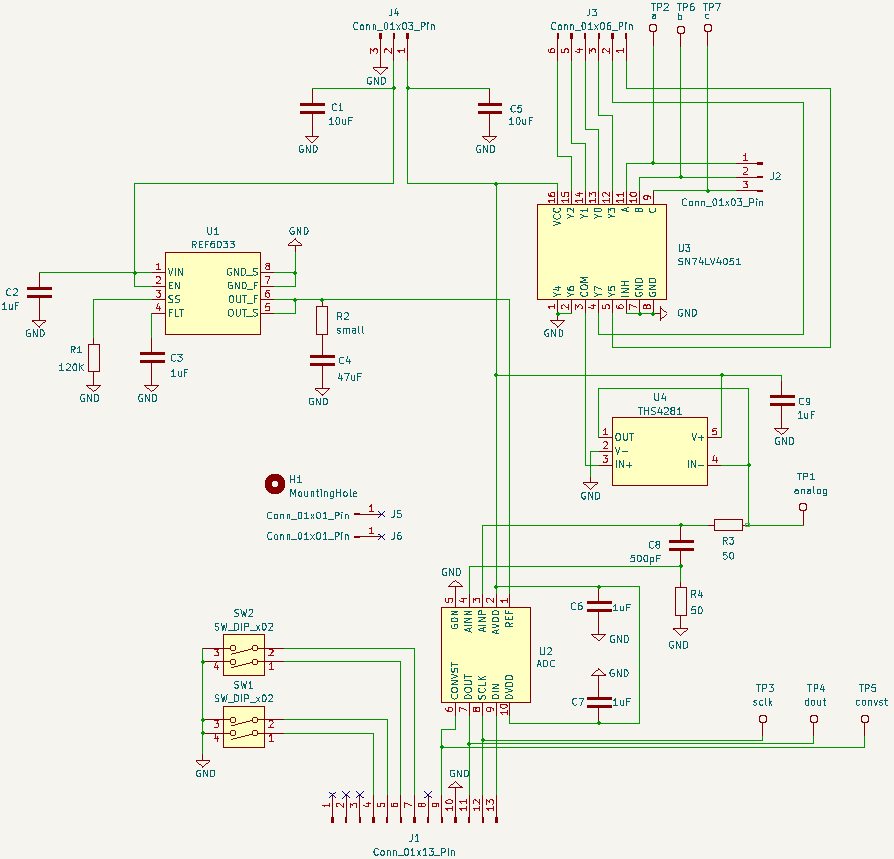
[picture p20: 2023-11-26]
hardware/releases/sca00/sca00_schematic.png

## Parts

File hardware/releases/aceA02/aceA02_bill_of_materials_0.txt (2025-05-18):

Label,  Description,                  Package,    Part Number,   Required?,    Est Cost,     Comment
-,      ACE A 0.2 circuit board,            -,              -,         Yes,       10.00,      -
J1,     1x8 connector socket 0.1in,         -,              -,         Yes,        0.16,      Solder to bottom side of circuit board.
J2,     1x8 connector pin 0.1in,            -,              -,         Yes,        0.16,      Solder to top side of circuit board.
J3,     1x2 connector socket 0.1in,         -,              -,         Yes,        0.16,      Solder to bottom side of circuit board.
J4,     1x8 connector pin 0.1in,            -,              -,         Yes,        0.16,      Solder to top side of circuit board.
J5,     1x8 connector pin 0.1in,            -,              -,         Yes,        0.16,      Solder to top side of circuit board.
J6,     1x8 connector socket 0.1in,         -,              -,         Yes,        0.16,      Solder to bottom side of circuit board.
J7,     1x8 connector pin 0.1in,            -,              -,         Yes,        0.16,      Solder to top side of circuit board.
J8,     1x2 connector socket 0.1in,         -,              -,         Yes,        0.16,      Solder to bottom side of circuit board.
J9,     1x8 connector pin 0.1in,            -,              -,         Yes,        0.16,      Solder to top side of circuit board.
J10,    1x8 connector pin 0.1in,            -,              -,         Yes,        0.16,      Solder to top side of circuit board.
R1,     4300 ohm resistor,               0805,   ERA-6AEB432V,         Yes,        0.25,      Resistor value depends on application, see documentation.
R2,     4300 ohm resistor,               0805,   ERA-6AEB432V,         Yes,        0.25,      Resistor value depends on application, see documentation.
R3,     4300 ohm resistor,               0805,   ERA-6AEB432V,         Yes,        0.25,      Resistor value depends on application, see documentation.
R4,     4300 ohm resistor,               0805,   ERA-6AEB432V,         Yes,        0.25,      Resistor value depends on application, see documentation.
R5,     4300 ohm resistor,               0805,   ERA-6AEB432V,         Yes,        0.25,      Resistor value depends on application, see documentation.
R6,     4300 ohm resistor,               0805,   ERA-6AEB432V,         Yes,        0.25,      Resistor value depends on application, see documentation.
R7,     4300 ohm resistor,               0805,   ERA-6AEB432V,         Yes,        0.25,      Resistor value depends on application, see documentation.
R8,     4300 ohm resistor,               0805,   ERA-6AEB432V,         Yes,        0.25,      Resistor value depends on application, see documentation.
R9,     4300 ohm resistor,               0805,   ERA-6AEB432V,         Yes,        0.25,      Resistor value depends on application, see documentation.
R10,    4300 ohm resistor,               0805,   ERA-6AEB432V,         Yes,        0.25,      Resistor value depends on application, see documentation.
R11,    4300 ohm resistor,               0805,   ERA-6AEB432V,         Yes,        0.25,      Resistor value depends on application, see documentation.
R12,    4300 ohm resistor,               0805,   ERA-6AEB432V,         Yes,        0.25,      Resistor value depends on application, see documentation.
R13,    4300 ohm resistor,               0805,   ERA-6AEB432V,         Yes,        0.25,      Resistor value depends on application, see documentation.
R14,    4300 ohm resistor,               0805,   ERA-6AEB432V,         Yes,        0.25,      Resistor value depends on application, see documentation.
R15,    4300 ohm resistor,               0805,   ERA-6AEB432V,         Yes,        0.25,      Resistor value depends on application, see documentation.
R16,    4300 ohm resistor,               0805,   ERA-6AEB432V,         Yes,        0.25,      Resistor value depends on application, see documentation.

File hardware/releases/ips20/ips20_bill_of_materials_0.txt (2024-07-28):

Label,  Description,           Package,    Part Number,          Required?,    Est Cost,     Comment
-,      IPS 2.0 circuit board, -,          -,                    Yes,          50.00,        -
U9,     SCA 0.0 circuit board, -,          -,                    Yes,              0,        Cost is in the SCA bill of materials.
C1,     10uF Ceramic,          0805,       C0805C106J8RAC,       Yes,           0.25,        X7R or better. 5% or smaller. 10 VDC or higher rating.
C2,     10uF Ceramic,          0805,       C0805C106J8RAC,       Yes,           0.25,        X7R or better. 5% or smaller. 10 VDC or higher rating.
C3,     0.1uF Ceramic,         0805,       C0805C104K3RACTU,     Yes,           0.25,        X7R or better. 5% or smaller. 10 VDC or higher rating.
C4,     1uF Ceramic,           0805,       C0805C105J4RACTU,     Yes,           0.25,        X7R or better. 5% or smaller. 10 VDC or higher rating.
C5,     10uF Ceramic,          0805,       C0805C106J8RAC,       Yes,           0.25,        X7R or better. 5% or smaller. 10 VDC or higher rating.
C6,     10uF Ceramic,          0805,       C0805C106J8RAC,       Yes,           0.25,        X7R or better. 5% or smaller. 10 VDC or higher rating.
C7,     10uF Ceramic,          0805,       C0805C106J8RAC,       Yes,           0.25,        X7R or better. 5% or smaller. 10 VDC or higher rating.
C8,     10uF Ceramic,          0805,       C0805C106J8RAC,       Yes,           0.25,        X7R or better. 5% or smaller. 10 VDC or higher rating.
C9,     10uF Ceramic,          0805,       C0805C106J8RAC,       Yes,           0.25,        X7R or better. 5% or smaller. 10 VDC or higher rating.
C10,    10uF Ceramic,          0805,       C0805C106J8RAC,       Yes,           0.25,        X7R or better. 5% or smaller. 10 VDC or higher rating.
C11,    10uF Ceramic,          0805,       C0805C106J8RAC,       Yes,           0.25,        X7R or better. 5% or smaller. 10 VDC or higher rating.
C12,    10uF Ceramic,          0805,       C0805C106J8RAC,       Yes,           0.25,        X7R or better. 5% or smaller. 10 VDC or higher rating.
C13,    10uF Ceramic,          0805,       C0805C106J8RAC,       Yes,           0.25,        X7R or better. 5% or smaller. 10 VDC or higher rating.
C14,    10uF Ceramic,          0805,       C0805C106J8RAC,       Yes,           0.25,        X7R or better. 5% or smaller. 10 VDC or higher rating.
D1,     LED - any color,       0805,       -,                    No,            0.50,        Any SMD LED in an 0805 package.
D2,     LED - any color,       0805,       -,                    No,            0.50,        Any SMD LED in an 0805 package.
D3,     LED - any color,       0805,       -,                    No,            0.50,        Any SMD LED in an 0805 package.
D4,     LED - any color,       0805,       -,                    No,            0.50,        Any SMD LED in an 0805 package.
D5,     LED - any color,       0805,       -,                    No,            0.50,        Any SMD LED in an 0805 package.
D6,     LED - any color,       0805,       -,                    No,            0.50,        Any SMD LED in an 0805 package.
D7,     LED - any color,       0805,       -,                    No,            0.50,        Any SMD LED in an 0805 package.
J1,     Barrel Jack,           -,          -,                    Yes,           1.00,        Any breadboard compatible should work.
J2,     Ethernet Jack,         -,          Cetus J1B1211CCD,     No,            5.00,        Header that comes in Teensy 4.1 Ethernet kit.  Only install if using Ethernet.
U13,    MIDI connector 5 pin,  -,          -,                    Yes,           1.00,        Breadboard compatible pin spacings (0.1 inch).
J3,     1x4 pin female 0.1in,  -,          -,                    No,            0.08,        Optional for a larger SCA card.
J47,    1x7 pin female 0.1in,  -,          -,                    No,            0.14,        Optional for a larger SCA card.
J48,    1x3 pin female 0.1in,  -,          -,                    No,            0.06,        Optional for a larger SCA card.
J11,    1x4 pin female 0.1in,  -,          -,                    No,            0.08,        Install if using display.
U12,    1x20 pin female 0.1in, -,          -,                    No,            0.40,        Install if using display.
J10,    1x2 pin male 0.1in,    -,          -,                    Yes,           0.04,        Install if need CAN Bus for board to board communication.
J12,    1x2 pin male 0.1in,    -,          -,                    Yes,           0.04,        For external power safety.
J46,    1x6 pin male 0.1in,    -,          -,                    Yes,           0.12,        Required for pedals.
-,      2x3 pin male 2mm,      -,          57102-S08-03LF,       No,            1.00,        Solder to Teensy for Ethernet connection.  2mm pitch.
-,      2x3 pin female 2mm,    -,          M22-7140342,          No,            1.50,        Solder to PCB for Ethernet connection.  2mm pitch.
-,      2x3 pin female 2mm,    -,          M22-7140342,          No,            1.50,        Stack on soldered 2x3 pin female 2mm for Ethernet connection.  2mm pitch.
J13,    1/4" connector,        -,          uxcell Audio 6.35mm,  Yes,           2.00,        Required for pedals.
J14,    1/4" connector,        -,          uxcell Audio 6.35mm,  Yes,           2.00,        Required for pedals.
J15,    1/4" connector,        -,          uxcell Audio 6.35mm,  Yes,           2.00,        Required for pedals.
J4,     1x8 pin male 0.1in,    -,          -,                    Yes,           0.16,        Header for connection to external sensors.
J5,     1x8 pin male 0.1in,    -,          -,                    Yes,           0.16,        Header for connection to external sensors.
J6,     1x8 pin male 0.1in,    -,          -,                    Yes,           0.16,        Header for connection to external sensors.
J7,     1x8 pin male 0.1in,    -,          -,                    Yes,           0.16,        Header for connection to external sensors.
J8,     1x8 pin male 0.1in,    -,          -,                    Yes,           0.16,        Header for connection to external sensors.
J9,     1x8 pin male 0.1in,    -,          -,                    Yes,           0.16,        Header for connection to external sensors.
J16,    1x8 pin male 0.1in,    -,          -,                    Yes,           0.16,        Header for connection to external sensors.
J17,    1x8 pin male 0.1in,    -,          -,                    Yes,           0.16,        Header for connection to external sensors.
J18,    1x8 pin male 0.1in,    -,          -,                    Yes,           0.16,        Header for connection to external sensors.
J19,    1x8 pin male 0.1in,    -,          -,                    Yes,           0.16,        Header for connection to external sensors.
J20,    1x8 pin male 0.1in,    -,          -,                    Yes,           0.16,        Header for connection to external sensors.
J21,    1x8 pin male 0.1in,    -,          -,                    Yes,           0.16,        Header for connection to external sensors.
J22,    1x8 pin male 0.1in,    -,          -,                    Yes,           0.16,        Header for connection to external sensors.
J23,    1x8 pin male 0.1in,    -,          -,                    Yes,           0.16,        Header for connection to external sensors.
J24,    1x8 pin male 0.1in,    -,          -,                    Yes,           0.16,        Header for connection to external sensors.
J25,    1x8 pin male 0.1in,    -,          -,                    Yes,           0.16,        Header for connection to external sensors.
J26,    1x8 pin male 0.1in,    -,          -,                    Yes,           0.16,        Header for connection to external sensors.
J27,    1x8 pin male 0.1in,    -,          -,                    Yes,           0.16,        Header for connection to external sensors.
J28,    1x8 pin male 0.1in,    -,          -,                    Yes,           0.16,        Header for connection to external sensors.
J29,    1x8 pin male 0.1in,    -,          -,                    Yes,           0.16,        Header for connection to external sensors.
J30,    1x8 pin male 0.1in,    -,          -,                    Yes,           0.16,        Header for connection to external sensors.
J31,    1x8 pin male 0.1in,    -,          -,                    Yes,           0.16,        Header for connection to external sensors.
J32,    1x8 pin male 0.1in,    -,          -,                    Yes,           0.16,        Header for connection to external sensors.
J33,    1x8 pin male 0.1in,    -,          -,                    Yes,           0.16,        Header for connection to external sensors.
J34,    1x8 pin male 0.1in,    -,          -,                    Yes,           0.16,        Header for connection to external sensors.
J35,    1x8 pin male 0.1in,    -,          -,                    Yes,           0.16,        Header for connection to external sensors.
J36,    1x8 pin male 0.1in,    -,          -,                    Yes,           0.16,        Header for connection to external sensors.
J37,    1x8 pin male 0.1in,    -,          -,                    Yes,           0.16,        Header for connection to external sensors.
J38,    1x8 pin male 0.1in,    -,          -,                    Yes,           0.16,        Header for connection to external sensors.
J39,    1x8 pin male 0.1in,    -,          -,                    Yes,           0.16,        Header for connection to external sensors.
J40,    1x8 pin male 0.1in,    -,          -,                    Yes,           0.16,        Header for connection to external sensors.
J41,    1x8 pin male 0.1in,    -,          -,                    Yes,           0.16,        Header for connection to external sensors.
J42,    1x8 pin male 0.1in,    -,          -,                    Yes,           0.16,        Header for connection to external sensors.
J43,    1x8 pin male 0.1in,    -,          -,                    Yes,           0.16,        Header for connection to external sensors.
J44,    1x8 pin male 0.1in,    -,          -,                    Yes,           0.16,        Header for connection to external sensors.
J45,    1x8 pin male 0.1in,    -,          -,                    Yes,           0.16,        Header for connection to external sensors.
-,      1x6 pin female 0.1in,  -,          -,                    Yes,           0.16,        SCA header. Top. Next to D6.
-,      1x3 pin female 0.1in,  -,          -,                    Yes,           0.16,        SCA header. Right. Next to R14 and J11.
-,      1x13 pin female 0.1in, -,          -,                    Yes,           0.16,        SCA header. Bottom. Next to D7 and R13.
-,      1x2 pin female 0.1in,  -,          -,                    Yes,           0.16,        SCA header. Left. Solder to 3.3v and 5v. Do not solder a connection to gnd location.
R1,     120  ohms,             0805,       ERA-6VEB1200V,        Yes,           0.75,        0.25W. 0.2% tolerance or better.
R2,     7500 ohms,             0805,       ERA-6AED752V,         No,            0.30,        For LED.  Can use smaller/larger value for brighter/dimmer LED.
R3,     7500 ohms,             0805,       ERA-6AED752V,         No,            0.30,        For LED.  Can use smaller/larger value for brighter/dimmer LED.
R4,     7500 ohms,             0805,       ERA-6AED752V,         No,            0.30,        For LED.  Can use smaller/larger value for brighter/dimmer LED.
R5,     7500 ohms,             0805,       ERA-6AED752V,         No,            0.30,        For LED.  Can use smaller/larger value for brighter/dimmer LED.
R6,     7500 ohms,             0805,       ERA-6AED752V,         No,            0.30,        For LED.  Can use smaller/larger value for brighter/dimmer LED.
R7,     47 ohms,               0805,       ERA-6AED470V,         Yes,           0.40,        0.125W. 5% tolerance or better. For IRIG signal.
R8,     47 ohms,               0805,       ERA-6AED470V,         Yes,           0.40,        0.125W. 5% tolerance or better. For IRIG signal.
R9,     100K ohms,             0805,       ERA-6AED104V,         No,            0.40,        0.125W. 5% tolerance or better. Required if using TFT display.
R10,    100K ohms,             0805,       ERA-6AED104V,         No,            0.40,        0.125W. 5% tolerance or better. Required if using TFT display.
R11,    100K ohms,             0805,       ERA-6AED104V,         No,            0.40,        0.125W. 5% tolerance or better. Required if using TFT display.
R12,       0 ohms,             0805,       RCA08050000ZSEA,      No,            0.10,        Any zero ohm resistor is ok. Required if using TFT display.
R13,       0 ohms,             0805,       RCA08050000ZSEA,      No,            0.10,        Any zero ohm resistor is ok. Required if using TFT display.
R14,       0 ohms,             0805,       RCA08050000ZSEA,      No,            0.10,        Any zero ohm resistor is ok. Required if using TFT display.
R15,    7500 ohms,             0805,       ERA-6AED752V,         No,            0.30,        For LED. Can use smaller/larger value for brighter/dimmer LED.
R16,    7500 ohms,             0805,       ERA-6AED752V,         No,            0.30,        For LED. Can use smaller/larger value for brighter/dimmer LED.
R22,    10 ohms,               0805,       10 ohm resistor,      Yes,           0.40,        0.125W. 20% tolerance or better. For pedals.
R26,    10 ohms,               0805,       10 ohm resistor,      Yes,           0.40,        0.125W. 20% tolerance or better. For pedals.
R29,    10 ohms,               0805,       10 ohm resistor,      Yes,           0.40,        0.125W. 20% tolerance or better. For pedals.
R23,    4700 ohms,             0805,       ERA-6AED472V,         No,            0.50,        0.125W. 5% tolerance or better. For pedals. Install if using passive pedals.
R25,    4700 ohms,             0805,       ERA-6AED472V,         No,            0.50,        0.125W. 5% tolerance or better. For pedals. Install if using passive pedals.
R28,    4700 ohms,             0805,       ERA-6AED472V,         No,            0.50,        0.125W. 5% tolerance or better. For pedals. Install if using passive pedals.
F1,     Fuse,                  1206,       -,                    Yes,           1.50,        User to decide.
F2,     Fuse,                  1206,       MFU1206FF00500P500,   Yes,           1.50,        0.5 amp fuse. User to validate.
SW1,    2 position switch,     -,          DS04-254-1-02BK-SMT,  No,            0.75,        Install if would like switch for configuration functions.
SW2,    2 position switch,     -,          DS04-254-1-02BK-SMT,  No,            0.75,        Install if would like switch for configuration functions.
TP5,    16:1 out,              -,          Keystone 500X,        No,            0.40,        Any breadboard header should work. This is a testpoint so optional.
TP6,    canh,                  -,          Keystone 500X,        No,            0.40,        Any breadboard header should work. This is a testpoint so optional.
TP7,    canl,                  -,          Keystone 500X,        No,            0.40,        Any breadboard header should work. This is a testpoint so optional.
TP8,    d1,                    -,          Keystone 500X,        No,            0.40,        Any breadboard header should work. This is a testpoint so optional.
TP9,    d2,                    -,          Keystone 500X,        No,            0.40,        Any breadboard header should work. This is a testpoint so optional.
TP10,   d3,                    -,          Keystone 500X,        No,            0.40,        Any breadboard header should work. This is a testpoint so optional.
TP11,   d4,                    -,          Keystone 500X,        No,            0.40,        Any breadboard header should work. This is a testpoint so optional.
TP12,   s0,                    -,          Keystone 500X,        No,            0.40,        Any breadboard header should work. This is a testpoint so optional.
TP13,   s1,                    -,          Keystone 500X,        No,            0.40,        Any breadboard header should work. This is a testpoint so optional.
TP14,   s2,                    -,          Keystone 500X,        No,            0.40,        Any breadboard header should work. This is a testpoint so optional.
TP15,   s3,                    -,          Keystone 500X,        No,            0.40,        Any breadboard header should work. This is a testpoint so optional.
TP19,   u1_i0,                 -,          Keystone 500X,        No,            0.40,        Any breadboard header should work. This is a testpoint so optional.
TP21,   gnd,                   -,          Keystone 500X,        No,            0.40,        Any breadboard header should work. This is a testpoint so optional.
TP22,   V3.3,                  -,          Keystone 500X,        No,            0.40,        Any breadboard header should work. This is a testpoint so optional.
U1,     16:1 multiplexer,      SOIC-24,    CD74HC4067,           Yes,           1.00,        Equivalent is ok.
U2,     16:1 multiplexer,      SOIC-24,    CD74HC4067,           Yes,           1.00,        Equivalent is ok.
U3,     16:1 multiplexer,      SOIC-24,    CD74HC4067,           Yes,           1.00,        Equivalent is ok.
U4,     16:1 multiplexer,      SOIC-24,    CD74HC4067,           Yes,           1.00,        Equivalent is ok.
U5,     16:1 multiplexer,      SOIC-24,    CD74HC4067,           Yes,           1.00,        Equivalent is ok.
U6,     16:1 multiplexer,      SOIC-24,    CD74HC4067,           Yes,           1.00,        Equivalent is ok.
U7,     Teensy4.1,             -,          -,                    Yes,          35.00,        To avoid soldering onto PCB use the two 1x24 headers (next two rows).
U7,     1x24 pin female 0.1in, -,          -,                    Yes,           0.48,        Solder onto PCB so can socket the Teensy instead of soldering the Teensy to PCB.
U7,     1x24 pin female 0.1in, -,          -,                    Yes,           0.48,        Solder onto PCB so can socket the Teensy instead of soldering the Teensy to PCB.
U8,     CAN Bus driver,        SOIC-8,     TCAN330G,             No,            3.50,        Install if need CAN Bus for board to board communication.
U11,    LDO voltage regulator, SOT-23,     TLV75533PDBVR,        Yes,           0.50,        5V-in. 3.3V-out. 500mA drive current. With overcurrent protection.
U15,    LDO voltage regulator, SOT-23,     TLV75533PDBVR,        Yes,           0.50,        5V-in. 3.3V-out. 500mA drive current. With overcurrent protection.
U16,    LDO voltage regulator, SOT-23,     TLV75533PDBVR,        Yes,           0.50,        5V-in. 3.3V-out. 500mA drive current. With overcurrent protection.
U17,    LDO voltage regulator, SOT-23,     TLV75533PDBVR,        Yes,           0.50,        5V-in. 3.3V-out. 500mA drive current. With overcurrent protection.
U18,    LDO voltage regulator, SOT-23,     TLV75533PDBVR,        Yes,           0.50,        5V-in. 3.3V-out. 500mA drive current. With overcurrent protection.
U19,    LDO voltage regulator, SOT-23,     TLV75533PDBVR,        Yes,           0.50,        5V-in. 3.3V-out. 500mA drive current. With overcurrent protection.
-,      Adafruit TFT LCD,      -,          Product ID 1770,      No,           30.00,        Install if using display. Connect display to J11 and U12.
H1,     Mounting hole 2.2mm,   -,          -,                    -,                0,        Nothing to install. just noting the mounting hole diameter for bolt selection.
H2,     Mounting hole 2.2mm,   -,          -,                    -,                0,        Nothing to install. just noting the mounting hole diameter for bolt selection.
H3,     Mounting hole 2.2mm,   -,          -,                    -,                0,        Nothing to install. just noting the mounting hole diameter for bolt selection.
H4,     Mounting hole 2.2mm,   -,          -,                    -,                0,        Nothing to install. just noting the mounting hole diameter for bolt selection.
H5,     Mounting hole 2.2mm,   -,          -,                    -,                0,        Nothing to install. just noting the mounting hole diameter - for SCA hold down.

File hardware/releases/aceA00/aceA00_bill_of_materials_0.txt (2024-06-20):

Label,  Description,                  Package,    Part Number,   Required?,    Est Cost,     Comment
-,      ACE A 0.0 circuit board,            -,              -,         Yes,       10.00,      -
J1,     1x8 connector socket 0.1in,         -,              -,         Yes,        0.16,      Solder to bottom side of circuit board.
J2,     1x8 connector pin 0.1in,            -,              -,         Yes,        0.16,      Solder to top side of circuit board.
J3,     1x2 connector socket 0.1in,         -,              -,         Yes,        0.16,      Solder to bottom side of circuit board.
J4,     1x8 connector pin 0.1in,            -,              -,         Yes,        0.16,      Solder to top side of circuit board.
J5,     1x8 connector pin 0.1in,            -,              -,         Yes,        0.16,      Solder to top side of circuit board.
J6,     1x8 connector socket 0.1in,         -,              -,         Yes,        0.16,      Solder to bottom side of circuit board (board label is not next to connector).
J7,     1x8 connector pin 0.1in,            -,              -,         Yes,        0.16,      Solder to top side of circuit board.
J8,     1x2 connector socket 0.1in,         -,              -,         Yes,        0.16,      Solder to bottom side of circuit board.
J9,     1x8 connector pin 0.1in,            -,              -,         Yes,        0.16,      Solder to top side of circuit board.
J10,    1x8 connector pin 0.1in,            -,              -,         Yes,        0.16,      Solder to top side of circuit board.
R1,     4300 ohm resistor,               0805,   ERA-6AEB432V,         Yes,        0.25,      0.125W. 1% tolerance or better.
R2,     4300 ohm resistor,               0805,   ERA-6AEB432V,         Yes,        0.25,      0.125W. 1% tolerance or better.
R3,     4300 ohm resistor,               0805,   ERA-6AEB432V,         Yes,        0.25,      0.125W. 1% tolerance or better.
R4,     4300 ohm resistor,               0805,   ERA-6AEB432V,         Yes,        0.25,      0.125W. 1% tolerance or better.
R5,     4300 ohm resistor,               0805,   ERA-6AEB432V,         Yes,        0.25,      0.125W. 1% tolerance or better.
R6,     4300 ohm resistor,               0805,   ERA-6AEB432V,         Yes,        0.25,      0.125W. 1% tolerance or better.
R7,     4300 ohm resistor,               0805,   ERA-6AEB432V,         Yes,        0.25,      0.125W. 1% tolerance or better.
R8,     4300 ohm resistor,               0805,   ERA-6AEB432V,         Yes,        0.25,      0.125W. 1% tolerance or better.
R9,     4300 ohm resistor,               0805,   ERA-6AEB432V,         Yes,        0.25,      0.125W. 1% tolerance or better.
R10,    4300 ohm resistor,               0805,   ERA-6AEB432V,         Yes,        0.25,      0.125W. 1% tolerance or better.
R11,    4300 ohm resistor,               0805,   ERA-6AEB432V,         Yes,        0.25,      0.125W. 1% tolerance or better.
R12,    4300 ohm resistor,               0805,   ERA-6AEB432V,         Yes,        0.25,      0.125W. 1% tolerance or better.
R13,    4300 ohm resistor,               0805,   ERA-6AEB432V,         Yes,        0.25,      0.125W. 1% tolerance or better.
R14,    4300 ohm resistor,               0805,   ERA-6AEB432V,         Yes,        0.25,      0.125W. 1% tolerance or better.
R15,    4300 ohm resistor,               0805,   ERA-6AEB432V,         Yes,        0.25,      0.125W. 1% tolerance or better.
R16,    4300 ohm resistor,               0805,   ERA-6AEB432V,         Yes,        0.25,      0.125W. 1% tolerance or better.

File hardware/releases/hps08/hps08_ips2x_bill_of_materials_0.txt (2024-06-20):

Label,   Description,           Package,    Part Number,          Required?,     Est Cost,     Comment
-,       HPS 0.8 circuit board, -,          -,                    Yes,           1.00,        -
R1,      180 ohm resistor,      0805,       ERA-6AED181V,         Yes,           0.25,        0.125W. 1% tolerance or better.
R2,      4300 ohm resistor,     0805,       ERA-6AEB432V,         Yes,           0.25,        0.125W. 1% tolerance or better.
U1,      CNY70 optical sensor,  -,          CNY70,                Yes,           1.00,        On back of PCB.
J0,      1x3 pin male 0.1in,    -,          -,                    Yes,           0.06,        -

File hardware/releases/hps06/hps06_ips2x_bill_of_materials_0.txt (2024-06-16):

Label,   Description,           Package,    Part Number,          Required?,     Est Cost,     Comment
-,       HPS 0.6 circuit board, -,          -,                    Yes,           1.00,        -
RV0,     Trimmer, 200 ohm,      -,          3224X-1-201E,         Yes,           5.00,        -
R1,      51 ohm resistor,       0805,       ERA-6AED510V,         Yes,           0.25,        0.125W. 5% tolerance or better. On back of PCB.
R2,      4120 ohm resistor,     0805,       ERA-6AEB4121V,        Yes,           0.25,        0.125W. 5% tolerance or better. On back of PCB.
U1,      CNY70 optical sensor,  -,          CNY70,                Yes,           1.00,        On back of PCB.
J0,      1x3 pin male 0.1in,    -,          -,                    Yes,           0.06,        -

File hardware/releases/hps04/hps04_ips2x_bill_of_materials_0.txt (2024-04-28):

Label,   Description,           Package,       Part Number,      Required?,     Est Cost,     Comment
-,       HPS 0.4 circuit board, -,             -,                Yes,           1.00,        -
R1,      180 ohm resistor,      through hole,  -,                Yes,           0.05,        0.125W. 5% tolerance or better.
R2,      4300 ohm resistor,     through hole,  -,                Yes,           0.05,        This value or slightly smaller.
U1,      CNY70 optical sensor,  -,             CNY70,            Yes,           1.00,        On back of PCB.
J0,      1x3 pin male 0.1in,    -,             -,                Yes,           0.06,        -

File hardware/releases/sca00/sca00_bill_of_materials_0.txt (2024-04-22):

Label,   Description,           Package,    Part Number,          Required?    Est Cost     Comment
-,       SCA 0.0 circuit board, -,          -,                    Yes,           7.50,        -
C1,      10uF Ceramic,          0805,       C0805C106J8RACAUTO,   Yes,           1.00,        X7R or better. 5% or smaller. 10 VDC or higher rating.
C2,      1uF Ceramic,           0805,       C0805C105J4RACTU,     Yes,           0.25,        X7R or better. 5% or smaller. 10 VDC or higher rating.
C3,      1uF Ceramic,           0805,       C0805C105J4RACTU,     Yes,           0.25,        X7R or better. 5% or smaller. 10 VDC or higher rating.
C4,      47uF Ceramic,          0805,       0805ZD476MAT2A,       Yes,           1.00,        X5R or better. 20% or smaller. 10 VDC or higher rating.
C5,      10uF Ceramic,          0805,       C0805C106J8RACAUTO,   Yes,           1.00,        X7R or better. 5% or smaller. 10 VDC or higher rating.
C6,      1uF Ceramic,           0805,       C0805C105J4RACTU,     Yes,           0.25,        X7R or better. 5% or smaller. 10 VDC or higher rating.
C7,      1uF Ceramic,           0805,       C0805C105J4RACTU,     Yes,           0.25,        X7R or better. 5% or smaller. 10 VDC or higher rating.
C8,      470pF Ceramic,         0805,       C0805C471J3RACTU,     Yes,           0.40,        X7R or better. 5% or smaller. 10 VDC or higher rating.
C9,      1uF Ceramic,           0805,       C0805C105J4RACTU,     Yes,           0.25,        X7R or better. 5% or smaller. 10 VDC or higher rating.
J1,      1x13 pin male 0.1in,   -,          -,                    Yes,           0.26,        Header for connection to IPS mainboard. Connect on back of PCB.
J2,      1x3 pin male 0.1in,    -,          -,                    Yes,           0.06,        Header for connection to IPS mainboard. Connect on back of PCB.
J3,      1x6 pin male 0.1in,    -,          -,                    Yes,           0.12,        Header for connection to IPS mainboard. Connect on back of PCB.
J4,      1x3 pin male 0.1in,    -,          -,                    Yes,           0.06,        Header for connection to IPS mainboard. Connect on back of PCB.
J5,      1x1 pin male 0.1in,    -,          -,                    No,            0.02,        Header for connection to IPS mainboard. Optional. Connect on back of PCB.
J6,      1x1 pin male 0.1in,    -,          -,                    No,            0.02,        Header for connection to IPS mainboard. Optional. Connect on back of PCB.
R1,      120K ohms,             0805,       ERA-6AED124V,         Yes,           0.50,        0.125W. 5% tolerance or better.
R2,      0.2 ohms,              0805,       ERJ-U6SFR20V,         Yes,           0.25,        Resistance less than 0.5 ohms. 0.125W. 5% or better tolerance.
R3,      47 ohms,               0805,       ERA-6AED470V,         Yes,           0.50,        0.125W. 5% tolerance or better.
R4,      47 ohms,               0805,       ERA-6AED470V,         Yes,           0.50,        0.125W. 5% tolerance or better.
SW1,     2 position switch,     -,          DS04-254-1-02BK-SMT,  No,            0.75,        Install if would like switch for configuration functions.
SW2,     2 position switch,     -,          DS04-254-1-02BK-SMT,  No,            0.75,        Install if would like switch for configuration functions.
TP1,     analog,                -,          Keystone 500X,        No,            0.40,        Any breadboard header should work. This is a testpoint so optional.
TP2,     a,                     -,          Keystone 500X,        No,            0.40,        Any breadboard header should work. This is a testpoint so optional.
TP3,     sclk,                  -,          Keystone 500X,        No,            0.40,        Any breadboard header should work. This is a testpoint so optional.
TP4,     dout,                  -,          Keystone 500X,        No,            0.40,        Any breadboard header should work. This is a testpoint so optional.
TP5,     convst,                -,          Keystone 500X,        No,            0.40,        Any breadboard header should work. This is a testpoint so optional.
TP6,     b,                     -,          Keystone 500X,        No,            0.40,        Any breadboard header should work. This is a testpoint so optional.
TP7,     c,                     -,          Keystone 500X,        No,            0.40,        Any breadboard header should work. This is a testpoint so optional.
U1,      2.5v reference,        VSSOP-8,    REF6025,              Yes,           7.50,        Select reference voltage based on maximum expected value from external sensor.
U2,      ADC. 1Msps. 16-bit,    VSSOP-10,   ADS8860,              Yes,          20.00,        Equivalent is ok.
U3,      8:1 multiplexer,       SOIC-16,    SN74LV4051,           Yes,           0.75,        Equivalent is ok.
U4,      op amp,                SOT-23-5,   THS4281,              Yes,           3.50,        Equivalent is ok.
H1,      Mounting hole 2.2mm,   -,          -,                    -,                0,        Nothing to install just noting the mounting hole diameter for bolt selection.

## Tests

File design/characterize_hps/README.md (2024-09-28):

# Hammer Position Sensor (HPS) System Characterization

## Purpose

Construct the *stem piano* measurement system response from experimental data. The measurement system response consists of:
* CNY70
* Hammer shank reflection properties
* Physical position and orientation of CNY70

Data is useful for understanding nonlinearities, noise, distortion, and tolerances of the hammer position measurement system.

## Setup

### stem piano
Code running on piano must include streaming raw analog-to-digital (ADC) counts over Ethernet. The *Stem Piano G* release supports this.

### Hammer Crane
Linear actuator and controller with an Arduino Nano. Actuator is attached by a thread to a hammer shank. Pulls shank up in a controlled manner.

### Analysis Code
Construct the measurement system response from *stem piano* measurements received over Ethernet while the *Hammer Crane* is moving the shank

## Running It!

### Getting Data

Attach a thread from the *Hammer Crane* to a hammer shank. Use a lightly attached piece of tape so that if the *Hammer Crane* accidentally tries to pull the shank past the hammer stop, it does not break the shank.

Turn on *stem piano*. Make sure *stem piano* is streaming raw ADC samples for the shank connected to *Hammer Crane*.

Run [analog_analysis/get_hammer_cal_data.py](analog_analysis/get_hammer_cal_data.py).

Start the *Hammer Crane* code. This lifts the hammer shank from resting position until contact with the hammer stop.

The measurement values are stored in *data/hammer_cal_data.txt*.

### Analyzing Data

Rename *hammer_cal_data.txt* to something describing the particular test setup. Record the test setup information in [data/README.md](data/README.md).

Run [analog_analysis/generate_analog_response.m](analog_analysis/generate_analog_response.m) from within Octave or Matlab. First edit the .m file so the data file name matches the file name selected in previous step.

The result is a curve of measurement system response vs. hammer shank position.

Optional: Run [analog_analysis/combine_analog_responses.m](analog_analysis/combine_analog_responses.m) from within Octave or Matlab. First edit the .m file so the data file names all matches the file names from previous tests.

The result is a set of measurement system responses vs. hammer shank position curves, resampled and normalized for comparison.

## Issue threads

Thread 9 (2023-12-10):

FW, ME: Selecting hammers/dampers in the IPS boards

davidedelvento, 2023-12-10:
Let's assume that one wants to have both hammers and dampers sensors. If my understanding is correct, current firmware require wiring *all* hammers (via SCA boards) to one IPS board and *all* dampers (again via SCA boards) to *the other* IPS board.

I think it would make it much easier wiring (shorter wires and less crossing cables) and much more efficient use of resources if each board could be configured (in firmware) to act as a hybrid hammers/dampers IPS for half the keyboard. The wiring is clear: you will be wiring only half the keyboard to one board, and the other half to the other board, halving the total length of the cables (potentially reducing noise when doing so, but I am not sure).

For the "more efficient use of resources" consider this scenario to begin: nothing is playing on the piano, both boards (and their ADCs in the SCA boards) are "frantically" sampling all sensors waiting for something to happen. Well, sampling the dampers is unnecessary, so that's the first waste, but that's not my main concern. The main concern is that sampling must be fast to make sure the latency between "key is played" and "MIDI signal is sent" is the lowest possible. Since the ADCs are multiplexed, we are not as fast as possible with the hardware we have. If a single board could be used to sample *both* hammers and dampers, the ADCs can be multiplexed at twice the frequency (because there is no need to check the damper until the note has been played), effectively having the ADC latency with no change in hw. Similarly, the software could probably be prevented from spending cycles checking the dampers until the note is played.

Of course this optimization cannot be used when a note is being held, because in such scenario it could be either re-played or it could be released and to detect what happens we must sample both the hammer and the damper sensor. But only about 10 notes can be held at a same time (given the players typically have 10 fingers), so *still* the optimization will work with 78/88 ~ 88% efficiency! It would be particularly useful if the dampers for one note will be assigned to a SCA board *different* from the corresponding hammer. Why? Because as described above when a note is held one has to monitor both hammer and damper and that would decrease the sampling rate when one needs it most, i.e. when the likelihood of repetitions and nearby note playing is highest.

Would this be extremely complicated with current firmware (which I have not studied yet) or is it doable? I'm willing to contribute to software and wiring scheme design if you deem it worthwhile.

gzweigle, 2023-12-10:
The present released code scans all 96 inputs every 400 microseconds (adc_sample_period_microseconds in hammer_settings.cpp).
My plan to go faster was more ADC on SCA, running in parallel (up to 6x fast is possible).
But agree, another approach is as described above.  No board spins needed.

gzweigle, 2024-06-10:
An advantage of present approach is single MIDI output.
Also, I have optimized the firmware to get the sample period down to 300 microseconds.

I've been playing the piano regularly for over half a year and the piano plays very well at this sample rate. Especially after fixing many sources of error (per YouTube video I recently posted).

My roadmap for faster sample rate remains the ADC parallelization on SCA, which requires only changes to the small, removable, SCA card.

The proposed architecture is very interesting but I in the interest of keeping the backlog small, I am considering to close this issue. Comments?

davidedelvento, 2024-06-10:
Yes, single MIDI out is highly desirable, but I don't see how it's relevant here? Probably just my ignorance here, this is what I am thinking: if you have separate hammer and damper boards each with 88 (or 96) channels, vs having two boards each one using half the keys but both hammers and dampers? If you need single MIDI out, in both cases the two boards need to communicate with each other and consolidate the output. If that consolidation code does not exist yet and it's not a priority to write it yet, in one case you have note-on from one board and note-off from another (which can be problematic for digital instruments), whereas in the other you have note-on and note-off from the same board (just for different note-number) which should be easier on the receiving size.

Moreover, IMHO, one big advantage of this approach is also the wiring: each board can be located closer to the relevant keys, simplifying wiring a lot.

Regarding your actual question about the ADC thing, I have no strong opinion, and the only opinion I have is not backed by data, since I have not been using a complete instrument as you have. I would just note that this aspect may be related to #55 but on that topic too you know that part better than I can comment.

So in conclusion, my opinion is that this is still a desirable feature to implement (leave the issue open), even though it may not be as important for some of the goals I originally mentioned, such as increase ADC rate (deprioritize).

gzweigle, 2024-06-10:
I am happy to leave open. I agree on the wire length benefit.

With present architecture, dampers are optional.  Just add a damper board (identical to hammer board). Nothing else changes.

With respect to MIDI - it is output from the hammer board only.  Damper measurements are sent over CAN bus from damper board to hammer board. Hammer board consolidates to a single MIDI output.  The dampers, as you correctly noted, require less resolution and so I was able to fit all damper data over the relatively slow CAN bus.

gzweigle, 2024-06-10:
Here is the damper board to hammer board code:

https://github.com/gzweigle/DIY-Grand-Digital-Piano/blob/main/firmware/releases/StemPianoIPS2/src/board2board.cpp

gzweigle, 2025-04-26:
Its been a while. All info remains in the issue history and can find with * search.

Closed 2025-04-26.

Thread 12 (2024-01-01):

Vref and sensor resistor

gzweigle, 2024-01-01:
I can get better accuracy by changing the SCA voltage reference part and the HPS load resistor value.

gzweigle, 2024-01-04:
bill of materials have been modified to change load resistor and reference.
Need to test with hardware before closing the issue.

Closed 2024-01-15.

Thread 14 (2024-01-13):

ME: note consistency

gzweigle, 2024-01-13:
repro:
Play multiple notes with same velocity. For example, using a ruler.
MIDI value is not exactly same for all notes.

soln:
Probably sensor consistency.
ADC - differential?

davidedelvento, 2024-01-14:
Again, https://github.com/jkominek/piano-conversion/wiki/Calibration-Procedure has some ideas on this. One could make the calibration procedure I described in #13 also ask for a fff strike and use that to calibrate the slope of the velocity computation. That is a bit tricky because while it's easy to raise the hammer to let-off without it going much higher, and it's also easy to have the hammer strike the sensor/string with "whatever" velocity, it's much harder to make it strike it with consistent velocity. I speculate (and my preliminary tests I described in the Mybrid repo confirm) that this calibration is not necessary once one has calibrated the let-off and the strike point and hence measured velocity only between these two values. But then I only had a handful of notes working, never a full set as you do, so I might be missing something, either on the user "feeling" side or on the sensor variability side. Also, my sensors different than yours and are probably mounted with a bit tighter tolerances, as you have probably already seen at https://pianoclack.com/forum/d/542-update-on-piano-conversion/

gzweigle, 2024-01-15:
I'm in the process of checking in details of a system I built to accurately measure sensor response.

gzweigle, 2024-04-20:
improved by a combination of rebuild/regulate action, redrill sensor bar with more accuracy, and real-time algorithm in firmware (code is in repo now)

Closed 2024-04-20.

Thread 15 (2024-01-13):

power supply noise

gzweigle, 2024-01-13:
repro:
Detailed measurements show quite a bit of 120 Hz noise.

soln:
Better +5V power supply.
Look at grounding.
Differential ADC.
Filters.

davidedelvento, 2024-01-14:
One of the most notably effect of power supply noise is on the intensity of the LED light, which in turns would cause a change of measured distance (unless it's very carefully calibrated, which IMHO is a big pain) with that frequency. That could turn out as a subtle modulation of the velocity at that frequency, since when we are in a peak intensity the hammers would appear to be closer (and hence hit the string/sensors earlier, and hence have a higher velocity/loudness) and the reverse when we are in a trough with hammers appearing more distance and etc-etc lower velocity/loudness.

See https://github.com/jkominek/piano-conversion/wiki/LED-Power-Board for a solution to this problem, which also has the added benefit to removing the needs of all those current-limiting resistors which are needless power sink. Not much each, but even a fraction of a watt when multiplied by 176 becomes non-negligible (that explain the lack of such resistors in my sensorboards as we were discussing elsewhere)

gzweigle, 2024-01-21:
Turns out this was due to ambient room lighting shining on the sensors.
With sensors shielded, the 120 Hz noise goes away.

Closed 2024-01-21.

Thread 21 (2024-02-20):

Video for "Piano Action Frame" is set to private

WebSnke, 2024-02-20:
Hi, I am a huge fan of this project and would love to build my own. However, the video for building the piano action frame is set to private.
Is this intentional or just a mistake?

davidedelvento, 2024-02-20:
Duplicate of #20

gzweigle, 2024-02-22:
https://github.com/gzweigle/DIY-Grand-Digital-Piano/discussions/22

WebSnke, 2024-02-23:
> Duplicate of #20

Yeah, noticed that too...
Btw, has anyone managed to put this into an upgright piano action?

davidedelvento, 2024-02-24:
> has anyone managed to put this into an upgright piano action?

That would be better for another issue or a discussion item e.g. on https://pianoclack.com/forum/

Hope Greg don't mind too much for me answering here instead. I don't think anybody has done that. In a nutshell, upright pianos have the following limitations:

* the action is harder to remove (not extremely hard, but harder than grand) and when removed, unless you have specialized equipment, you are guaranteed to break it because it you cannot lay it in any position without having the whole weight pushing on a brittle part, unlike in a grand where you can just pull it out and place it on any table
* the keyboard is part of the cabinet and cannot be removed, if not one key at the time (and then you need to rebuild a keyframe), unlike in a grand where the keyboard is attached to the action
* if you want to reuse the upright cabinet you may want to remove the harp to make it lighter. This is close to impossible (unlike in a grand, where it is easy if you have a hoist, and demanding but not too hard if you work with *several* people in the operation)
* if you don't remove the harp, you have to remove all the strings, which is a very long, tedious and dangerous job -- at that point you have very limited working space for the sensors. Again, not impossible, but much harder than a grand
* assuming that you succeed in all of the above, you end up with an arguably inferior action than a grand, after having done much more work -- hence I don't see why one would embark in such an endeavor.
* anticipating an answer of "but I don't have room for a grand in my house", my comment is "me neither" and in fact I made an "upright" (actually a spinet) out of a grand action. That was EASY. See https://pianoclack.com/forum/d/170-build-your-own-hybrid-piano-step-two-the-cabinet for details.

WebSnke, 2024-02-24:
Thanks for your response. Let's continue this on the forum.

Closed 2024-02-20.

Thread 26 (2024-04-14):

HW: pedal voltage exceeds Vref

gzweigle, 2024-04-14:
The pedal inputs have pullups to VDD.
Two problems:
1. clipping at ADC.
2. The ADC max input is Vref + 0.3V.

The firmware handles this ok. Its been working for months.

However, should add a resistor to IPS 2.0 PCB to keep voltage in range 0 to Vref.
Use design from first architecture:
https://youtu.be/9sqkgVXceJU?t=63

gzweigle, 2024-04-16:
Looks like I can fix this, without changing any existing PCB, by making a tiny removable resistor divider board that snaps on IPS.
Because fortunately I connected the pedals through a header.
In hindsight, this is the preferred approach anyway because VREF is configurable.
Missing the impact of configurable VREF on pedals is what caused the "hardware bug".
So, need a configurable pedal output voltage. Hence the new board.
In process of building and testing the idea.

gzweigle, 2024-06-09:
Added the hardware files and updated the documentation.

Closed 2024-06-09.

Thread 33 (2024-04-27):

HW: higher current LDO

gzweigle, 2024-04-27:
1.75A / 6 = 291mA which is too close to the 300mA in parts list.

gzweigle, 2024-04-27:
Consider TLV755P (500mA) in place of existing TLV733P (300mA).  Also increase input / output capacitance.

The stem piano documentation says 1.75A. The test results were 1.5A.

1.5A / 6 = 250mA < 300mA LDO.

However, one of the LDO is also powering the SCA.

gzweigle, 2024-04-28:
More clearly explain HPS current constraints:
https://github.com/stem-piano/stem-piano-g-main/blob/main/documentation/component_manual.md

Add HPS current measurement table:
https://github.com/gzweigle/DIY-Grand-Digital-Piano/tree/main/hardware/releases/hps07

Closed 2024-04-28.

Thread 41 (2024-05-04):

HW: no sca connector labels on ips

gzweigle, 2024-05-04:
The ips parts list does not include the four sca socket connectors.
Missed it because used a custom symbol in schematic, resulting in no connector labels on ips board.

gzweigle, 2024-06-15:
added to bill of materials for ips20

Closed 2024-06-15.

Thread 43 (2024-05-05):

HW: location of sensor resistor

davidedelvento, 2024-05-05:
I am wondering if you have considered putting the sensor resistor after the multiplexers, so you would not need to have (solder) 88 of them.
In my case that's obviously because I don't want to modify my sensorboards which have been already fabricated without, and I don't want to massively change your main board either with 88 resistors. Obviously I could have them in the cables and that might be my chosen route, but putting them after the multiplexer seems also doable, so asking if you considered that (and perhaps discarded it for some reasons).

gzweigle, 2024-05-05:
I ran SPICE simulations of various options last year.
Settling time (to ADC resolution) limits the sample rate of every option.
So I need the circuit to settle as quickly as possible.
CNY70 trying to drive through multiplexers slowed things down too much.
An amp (ie TIA) improves the no-resistor settling time problem but only if before the multiplexers, then need 88 amplifiers.
Key goal of stem piano G is lowest possible cost.

However, stem piano G is pretty much done. Maybe next piano should be with amps vs. R.

For reference, these diagrams show the ADC timings, although not the settling time simulations:
https://github.com/gzweigle/DIY-Grand-Digital-Piano/blob/main/design/data_acquisition/eca0X_ips2X/eca0X_ips2X_timing_design.md

davidedelvento, 2024-05-05:
Yes, that's exactly what I had in mind, but just as "gut feeling". So with current design it is better to put the resistors in between the multiplexers and the sensors.

> An amp (ie TIA) improves the no-resistor settling time problem but only if before
> the multiplexers, then need 88 amplifiers. Key goal of stem piano G is lowest possible cost.

Well, using TIA is not too bad, many IC have several op amps in the same package and cost only pennies. FWIW, that's what https://github.com/jkominek/piano-conversion/ intend(ed?) to use see https://github.com/jkominek/piano-conversion/wiki/Analog-Stage-Theory-of-Operation#transimpedance-amplifier
In fact I might for intermediate board(s) on which I will mount resistors for now and which I will replace with a TIA later.

Maybe for the next version of the sensorboards you may do the same so you will increase flexibility (i.e. not require replacing 88 expensive sensorboards) if one decides to switch between options.

Thanks for the discussion!

gzweigle, 2024-05-05:
Thanks. Agree.

Closed 2024-05-05.

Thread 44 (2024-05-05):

FW: option to use optical sensors for pedals

davidedelvento, 2024-05-05:
In your design you have 3 jacks for external pedals. In a full DIY grand (such as the one I have built), one may want to use the original pedals and use the same optical sensors (properly mechanically adjusted for the pedal travels) instead. Since the design already has 96 channels and most pianos have 88 keys, it should be easy to allocate 1, 2 or 3 channels to the pedals.

gzweigle, 2024-05-05:
Yes that will work.
Cases like that are exactly why I put header J46. Can bypass the jacks for up to 8 pedals.
See pedal section of:
https://github.com/stem-piano/stem-piano-g-main/blob/main/documentation/assembly_manual.md
Skip the wires, connect direct to J41, 43, 45.

davidedelvento, 2024-05-05:
Oh, I missed that, it's great!
So it's already supported in firmware?

gzweigle, 2024-05-05:
Just minor firmware changes.

davidedelvento, 2024-12-15:
I attempted to get this to work in the most naive way, and I went nowhere. Before I spend too much time going in the wrong direction, and reverse engineering what you have done, can you please nudge me towards what you had in mind here?

My pedal sensors are identical to your key sensors, so I need the three-way connector (I see that in the wiring diagram you connect only two). Also, it (wrongly?) appears to me that you wire two ADC channel per pedal, but one of such channel is just a "flag" and currently not in use. Is that right?

TIA!

gzweigle, 2024-12-15:
Yes the pedal jacks have two outputs.
One output is the pedal analog signal.
The other output is an optional indicator "flag" that the pedal is connected.

On the IPS 2.0 circuit board, each output goes to a separate ADC channel.
And, yes, correct, the pedal connection indicator "flag" is not used by the firmware.

Connecting a pedal directly to the header at the back of the IPS 2.0 circuit board should work.  Since all the pedal jack is doing is writing to one of the ADC channels.

davidedelvento, 2024-12-16:
Thanks, so to confirm:

1. I don't have to change anything in the multiplexer code, that channel is already read by the default multiplexing settings of the firmware
2. The power is also properly connected so if I attach a key sensor (equivalent to your HSB, not mine which has external power) to the pedal channel, that key should act as a pedal -- and if I don't see any MIDI pedal message that's a problem with either wiring or sensor (not firmware)

Correct?

gzweigle, 2024-12-16:
(1) - There is a setting for which ADC channel routes to the pedal algorithm in the firmware.  The setting allows any of the 96 inputs to be used for pedal(s).
https://github.com/gzweigle/open-hybrid-piano/blob/main/firmware/releases/ips2_hammer/hammer_settings.cpp

(2) - The HPS sensors require 3.3V and ground connections so those two of the three IPS/HPS pins are "outputs" to the HPS. If your pedal gets power by another means, then only one connection is required from the pedal to the IPS board.

Note that pedals with a passive variable resistor will need some way to bias and set the proper output voltage to the ADC.   This is the purpose of the pedal level shift (PLS) card.
https://github.com/gzweigle/open-hybrid-piano/tree/main/hardware/releases/pls00

davidedelvento, 2024-12-16:
(1) perfect thanks

(2) I must not have explained myself -- My pedal is not a digital piano pedal (neither active nor passive). My pedal is the original pedal from the acoustic piano I took the action from! I have installed an HPS into it. As such it does need power and ground.

Given what you wrote in (1) I assume that from the hardware perspective those additional pins are correctly wired to power and ground and if my pedal is not working (which is the case) something else in the wiring or in the sensor must be wrong. Next weekend I will start debugging from there

Thanks!

davidedelvento, 2025-01-04:
Is it supposed to output continuous values? Looking at the code I'd say yes, but....

I managed to get it to work, but it outputs only 0 or 127 on CC64 (sustain). Have you tried hooking one of the optical sensors and verified it gives intermediate values too?

Closed 2024-05-05.

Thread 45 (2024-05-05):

HW: LDO current

gzweigle, 2024-05-05:
LDO in parts list is ok but realized that if want an expanded SCA in future, it could require more current.
Better to find a larger part, test it, then put in parts list.

gzweigle, 2024-06-15:
In the ips20 bill of materials:
(1) replace the 300mA TLV73333PQDBV with 500mA TLV75533PDBVR.
(2) replace the 1uF LDO capacitors with 10uF. Input and output.

Solder a replacement of one new LDO on IPS 2.0 (U11).  Test.
The max current increases and also tests show get slightly better noise performance.

Link:
https://github.com/gzweigle/DIY-Grand-Digital-Piano/blob/main/hardware/releases/ips20/ips20_bill_of_materials.txt

Closed 2024-06-15.

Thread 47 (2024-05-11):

FW: cal rare outlier

gzweigle, 2024-05-11:
Get an outlier that breaks calibration for a single note.
Happens very rarely.

davidedelvento, 2024-05-11:
What do you mean by "breaks calibration"?

gzweigle, 2024-05-11:
The firmware is now automatically compensating for sensor nonlinearity.

Its a huge improvement over the problems I described in my last YouTube video.

(for my skill level) the piano "regulation" is now very good.  And, I have ideas to make even better too.

However, on rare occasions a note will go out of calibration. Then that note sounds slightly louder or quieter than others. My guess is: either a firmware bug or unexpected/unknown noise.

Code link:
https://github.com/gzweigle/DIY-Grand-Digital-Piano/blob/main/firmware/releases/StemPianoIPS2/src/calibration_sensor.cpp

davidedelvento, 2024-05-11:
Ah, very nice! I am preparing/purchasing what I need to finally solder/assemble one (still need to figure out the PCB order), and I hope that by the end of June I will be able to contribute something more specific to (minor) issues like this!!

gzweigle, 2024-05-11:
cool.
I need to get a few very minor HW changes in.

Also, slowly migrating to a GitHub organization https://github.com/stem-piano/

Going slow because of all the links to original.

gzweigle, 2024-08-10:
Can't repro

Closed 2024-08-10.

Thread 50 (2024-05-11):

HW: add ground pin to J46

gzweigle, 2024-05-11:
In support of https://github.com/gzweigle/DIY-Grand-Digital-Piano/issues/26, adding a ground pin to J46 cleans things up.
Board will work without this.

gzweigle, 2024-06-15:
Merge to https://github.com/gzweigle/DIY-Grand-Digital-Piano/issues/52

Closed 2024-06-15.

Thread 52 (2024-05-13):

HW: new IPS 2.1

gzweigle, 2024-05-13:
Presently working on a new iteration of the IPS mainboard.
Goal: all changes compatible with existing IPS 2.0 firmware.

Moving CAN connector to rear of board.
Adding another LED/testpoint to front by Teensy (making TFT IRQ optional with a jumper resistor).
Putting extension SCA power on main 3.3V instead of an LDO 3.3V.
Move J46 to right.

Investigating adding 96 optional 805 surface mount resistors to bottom side of board in support of another sensor approach:
https://github.com/stem-piano/sensor-systems/tree/main/qps

Addressing these existing issues:
(1) Adding ground pin to J46
https://github.com/gzweigle/DIY-Grand-Digital-Piano/issues/50
As optional gnd connect point for new PLS board: https://github.com/gzweigle/DIY-Grand-Digital-Piano/issues/26
(2) Adding SCA connector labels
https://github.com/gzweigle/DIY-Grand-Digital-Piano/issues/41
(3) BOM - changing LDO part
https://github.com/gzweigle/DIY-Grand-Digital-Piano/issues/45

davidedelvento, 2024-05-13:
Awesome!!
If it's not too many irons in the fire, maybe investigate adding some TIAs. If they need to be before the mux (and hence be 96 of them) perhaps it's better to make an interposer board. If they can be after the mux (and hence just a hanful) putting them on the IPS makes more sense. We'd need to run some simulation (if you haven't already)

gzweigle, 2024-06-08:
> perhaps it's better to make an interposer board

Good point.  Will use the 96 sensor headers.  Created issue: https://github.com/gzweigle/DIY-Grand-Digital-Piano/issues/53

Therefore:
- Removing the 96 805 surface mount resistors from scope of IPS 2.1.
- These (and optional TIA) will be on the new removable sensor interface boards.

This means that, while IPS 2.1 has some nice improvements, its not necessary.  The existing IPS 2.0 is ok.  So, likely I will lower the priority of creating IPS 2.1.

gzweigle, 2024-06-15:
Updated list of changes from IPS 2.0 to IPS 2.1:
(1) Move CAN connector next to quarter inch jacks.
(2) Add another LED/testpoint to front by Teensy (making TFT IRQ optional with a jumper resistor).
(3) Put extension SCA power on main 3.3V instead of an LDO 3.3V.
(4) Move J46 to right to make room for CAN.

(5) Add ground pin to J46: https://github.com/gzweigle/DIY-Grand-Digital-Piano/issues/50
(6) Adding SCA connector labels: https://github.com/gzweigle/DIY-Grand-Digital-Piano/issues/41

IPS 2.1 is on hold because these improvements are minor.

gzweigle, 2024-06-23:
Another addition for IPS 2.1. Jumper on R23, R25, and R28 so can use active or passive pedals without having to change whether resistors are soldered onto the board.

gzweigle, 2024-07-01:
Another one - for both Teensy and SCA, include the headers in the schematic.

gzweigle, 2024-07-12:
Another one - external connection for a USB MIDI port in addition to the serial MIDI port.

gzweigle, 2024-07-12:
More improvements for IPS 2.1:
The +5V - USB power info printed on the circuit board are overly restrictive.
Could also add information like this on back of board?

davidedelvento, 2024-07-13:
Since you are planning to redo this, in my opinion is better to do as vagfilm mentioned: replace all of these with just headers and let all the jacks to be "floating". This will greatly simplify assembly, allow more flexibility, and provide the option to build a nice enclosure where the jacks can be safely attached without risk of stressing/ruining the PCB by continued use.

gzweigle, 2024-07-13:
Its a good idea to make a version with a smaller PCB, no TFT or quarter inch inputs.

Note that presently all 96 inputs are independently available along the back of the PCB. The quarter inch jacks connect only to header J46 and nothing else. Does that answer the first question?

davidedelvento, 2024-07-13:
> Its a good idea to make a version with a smaller PCB, no TFT or quarter inch inputs.

Agreed. I would go as much as to not have Ethernet, MIDI, power supply jack or anything. But I don't mean that these are not possible, just that they are not directly attached to the board. In fact, I think all of them (including the TFT) would be at least "nice to have" if not "absolutely needed" but the design could be better served if all of them are attached to the board via a ribbon cable and then mechanically held somewhere else (e.g. in the enclosure).

> Note that presently all 96 inputs are independently available along the back of the PCB.
> The quarter inch jacks connect only to header J46 and nothing else.
> Does that answer the first question?

I guess you mean the other ticket? If so, yes. In this issue report I didn't have any question in my ticket only a suggestion (which you are free to consider or reject as you see fit, obviously).

gzweigle, 2024-07-14:
Interesting idea... I could put everything optional, or that could have variants, with cable connectors.

gzweigle, 2024-07-26:
Info on circuit board include to cut 5V pad

gzweigle, 2024-09-02:
Add USB host connection

gzweigle, 2024-09-02:
For USB host - see this discussion: https://github.com/gzweigle/DIY-Grand-Digital-Piano/issues/6

technolhodgy, 2024-09-02:
I have been keeping up with you Youtube Video's
This is a great project, and I look forward to seeing it progress.

I picked up a Grand Action last year that was going to be broken down.
I have just about had an octave working on a Pi Pico, and plan to scale it up to 88 notes soon.

gzweigle, 2024-09-07:
Consolidated change list (so far!) to consider for a future IPS 2.1 board spin, along with a few additional items:

Features:
USB MIDI (I think it has to be host?) connection.
Quarter inch jack interposer board instead of presently forcing specific quarter inch jack types.
Push button in addition to switches.
Dedicated TFT processor with fast command-based processor2processor interface.

Improvements:
Move CAN connector to back of board.
J46 – move to make room for CAN.
Add another LED/testpoint to front by Teensy (making TFT IRQ optional with a jumper resistor).
Put extension SCA power on main 3.3V instead of an LDO 3.3V.
J46 – add ground pin.
Jumper on R23, R25, and R28 so can use active or passive pedals through the quarter inch jacks without solder change.
Socket the fuse.
TFT LDO.
Move Teensy forward

Labels:
SCA connector labels.
For both Teensy and SCA, include the headers in the schematic.
New +5V - USB power info on circuit board.
Put additional instructions on back silkscreen.

Fixes:
Add external pullups to switches (addressing a Teensy problem).

General:
Could I keep it "99%" compatible with IPS 2.0 codebase?

davidedelvento, 2024-09-08:
> USB MIDI (I think it has to be host?) connection.

- [ ] No why do you want to make host? A keyboard is a device and so this should be.
- [ ] I have other things to discuss but let me open a separate issue for them, not to pollute this one with discussion but leaving it just as a list of things which you will have concluded are worth implementing -- in fact I will delete this comment if you ask me to, so we keep this issue clean
- [ ] speaking of lists, see how you can make it very nicely? Click on the "checklist" icon to the left of the paperclip (you should be able to edit your earlier message)

gzweigle, 2024-09-21:
See if can make space for stickers next to LED.  Then, a user can make it easy to identify the LED function based on the firmware.

gzweigle, 2024-09-28:
Moving the comment from issue https://github.com/gzweigle/DIY-Grand-Digital-Piano/issues/94 to this consolidated ips 2.1 changes issue.

"The silkscreen for the IPS should include a text saying if the + is inside or outside"

gzweigle, 2025-05-04:
Consider swapping 3.3v and gnd rows at sensor header to simplify wiring in some cases.
See: https://github.com/gzweigle/open-hybrid-piano/issues/96

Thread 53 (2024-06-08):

HW: sensor interface boards

gzweigle, 2024-06-08:
Realized that I can use the 6 header sets on back of IPS mainboard:
(1) J4-J9
(2) J16-J21
(3) J22-J27
(4) J28-J33
(5) J34-J39
(6) J40-J45

To socket 6 small, identical sensor interface printed circuit boards.

Removable.

These can translate any sensor front end interface. Without changes to the IPS mainboard. This makes the system very flexible for any sensor front end or processing in front of the ADC.

For example, put burden resistors or TIAs on the new sensor interface boards.

In process of creating PCB for a few interface options.

gzweigle, 2024-06-20:
The interposer board with resistors is done and tested.
Hardware location:
https://github.com/gzweigle/DIY-Grand-Digital-Piano/tree/main/hardware/releases/aceA00
Instructions:
https://github.com/stem-piano/stem-piano-g-main/blob/main/documentation/assembly_manual.md

Closed 2024-06-20.

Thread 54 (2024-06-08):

HW: change pedal TN pulldown resistor values

gzweigle, 2024-06-08:
The uxcell Audio 6.35mm 1/4 inch pedal connector has two outputs:

T and TN.  Pedal inputs drive the T output.

- T and TN are shorted together when no pedal is connected.  The purpose is that, by grounding TN, it prevents noise on T when a pedal is not connected. This doesn't matter as much to stem piano because T output is processed in firmware. T output does not connect directly to any audio.

- T and TN are open circuited when a pedal is connected.

I put a 100Kohm resistor in the bill of materials for the TN pulldown: R22, R26, R29.

However, that is too much for the SAR ADC. So, TN winds up following T because of the muxing order.

This makes it difficult for the firmware to determine if a pedal is connected.

Its better to connect these TN outputs to ground.  Or, if want a little safety in case of circuit or other error, use a small pulldown resistance for R22, R26, R29.

gzweigle, 2024-06-15:
Test using 10 ohms.
Solder onto an ips20 board and test.
Tests show that the TN stays at ground.

Closed 2024-06-15.

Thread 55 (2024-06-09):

FW: improve the velocity algorithm

gzweigle, 2024-06-09:
During testing and creating most recent video on note-to-note consistency, I notice the reported velocity is less consistent than the hammer position. Probably due to the derivative in algorithm. I have a few ideas to improve and need to get into the code.

davidedelvento, 2024-06-10:
IMHO, the main problem here is how to get a "ground truth" on which to assess the algorithm, and then find the root cause to the inconsistencies. Some questions for you to consider (in addition to what you are already thinking about)
* Is single note velocity always "perfect" for some way of considering perfection? \
* Do you still have the single note action which you could use for testing? Can you install two sensors for that same key and see how they differ from each other, ruling out difference in mechanics/regulation from the noticed difference in measured velocity?

gzweigle, 2024-06-22:
Discoveries/Improvements so far:

(1) For slow strike (quiet note) cannot use the max() algorithm because the hammer travel is under tighter control of pianist than when fast strike (louder note). This could explain why sometimes the piano feels inconsistent when playing ppp. Use a window back from strike point.

(2) Should not use the velocity zero crossing as time of strike because derivative has timing variations susceptible to signal asymmetry. Even though it is linear phase. I have another algorithm.

(3) Tests and data are indicating that the type of foam used for hammer stop may play a bigger role in velocity accuracy than I initially assumed.

None of this in GitHub code yet.

gzweigle, 2024-07-07:
Details of the existing and improved velocity algorithms will be covered in the technical paper:
https://github.com/gzweigle/DIY-Grand-Digital-Piano/issues/73

gzweigle, 2024-08-10:
Added a second algorithm.

Algorithm 0: No thresholds. Less dependent on precise mechanical setup. Longer delay. Less accurate.
Algorithm 1: Uses thresholds. Requires a mechanical setup with tight tolerances. Minimal delay and more accurate.
May add more algorithms in future

Closed 2024-08-10.

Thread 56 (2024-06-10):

On-board ADC usage?

szbergeron, 2024-06-10:
Is there a reason for specificallly using an external ADC for the stem piano, instead of the two on-board ADCs on the teensys?
I've been working on a stem-piano-inspired build with hall effect sensors, and wasn't sure if there's some hidden gotcha I haven't seen. So far, I've been able to push the sample rate high enough that even doing all 88 keys off of one teensy should be fine, but have planned in a leaf/hub architecture anyway just for some extra flexibility

gzweigle, 2024-06-11:
Sounds like a fun and interesting project.

The Teensy ADC is probably ok.

This is because the ADC is likely not the dominant error source. There are many other error sources (I recently listed on the youtube channel).

As for stem piano, it streams all hammer positions over Ethernet. So, I like the 16-bit ADC because with offline processing I can use more sophisticated algorithms to analyze the waveforms.  For what purpose I don’t know yet.

davidedelvento, 2024-06-11:
As Greg said, the internal ADCs are probably okay, but using an external, better ones frees more board resources and eliminate *possible* source of inaccuracies. Whether or not such inaccuracies is debatable and require studying. This is what Jay is doing at https://github.com/jkominek/piano-conversion/discussions/58

So to start your experimenting, you can definitely use the internal ADCs as I have done for example with https://github.com/davidedelvento/Mybrid/tree/main (and Jay has done with the STM32). That may turn out to be "perfect", or "adequate with some limitations" or "not good enough", depending on your goals. In my opinion, the goal of a project like this is to get the very best possible setup (ideally much better than commercial products) with an expense that is relatively inexpensive compared to commercial Hybrid pianos -- hence the use of an external ADC makes sense. If your goal is maximum simplicity or minimal expense, the internal ADC makes more sense. In either case, studying it is very appropriate, so please do share what you find!

szbergeron, 2024-06-14:
Neat, I'm definitely tending toward an "opinionated and functional" thing more than something that gives me all the extra analytics. Using the dual ADCs in parallel I've found gives me about 16 keys (a "batch" to sample) per 40 microseconds or so, and with muxes and key attention I might be able to get this down to just a single teensy, said muxes, some op-amps, and my sensors on a few daisy-chained boards for all 88 keys and assorted controllers.

I'm not really doing this for money-saving, I'm just kind of a dumbass so the less EE work I touch the better. My goal is to do more magic in software to offset for simpler hardware. So far, doing a linear regression of the hammer velocity between let-off and when it "hits the string" with a buffer gap on either end gives me quite stable results, especially with 300+ samples in that distance at what I'd consider "fortissimo" with a single key and attention. I still want to improve SNR a bit so I'm going to try some op-amps to boost the input from the sensors, but that might just be vanity more than anything legitimately necessary

davidedelvento, 2024-06-15:
To avoid reinventing the wheel, consider https://github.com/jkominek/piano-conversion/wiki/Analog-Stage-Theory-of-Operation -- Jay recently also commented that such an configuration is not giving the expected/hoped results, but I can't find that comment now, so you have to dig into the repo looking for his latest verbiage and check exactly what the sentence says, rather than trusting my second-hand report

szbergeron, 2024-06-15:
My read is that the problem is the observed output impedance of the phototransistor in the CNY70? The [1302](https://www.jameco.com/Jameco/Products/ProdDS/2135881.pdf) sensors I'm using only have 5 ohm output impedance at 1ma, and is a powered device with internal amplification already. I'm no EE person, so I'm sorta trying to navigate the runes as I go, but my impression was that stacking op-amps was already relatively common so pairing the internal one with an additional stage should be "fine"? I'm sure I'd run into more issues if I tried to plop an optical sensor in place of hall effect, so my idea of being "sensor agnostic" probably goes out the window. Hall effect seems quite noise free when I use stronger magnets for each key though so fingers crossed I can double down and it turn out ok.

szbergeron, 2024-06-15:
I also realized checking the datasheet for the a1302 again that it really wants a 5v supply, I tried a quick and dirty test and the half-range output at 5v (from 0 measurable field to magnet in contact with sensor) is a much more sensible range so long as I can limit the other side of the range from overvoltage. It does mean 2 power rails, but I can make that happen

Closed 2024-07-21.

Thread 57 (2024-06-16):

HW: resistor type

gzweigle, 2024-06-16:
A few thick film resistors where thin film is better.

hps06_ips2x_bill_of_materials.txt, hps07_ips2x_bill_of_materials.txt:
CRCW080550R0FKTA (50 ohm thick film resistor) replace with ERA-6AED510V (51 ohm thin film resistor).

hps08/hps08_ips2x_bill_of_materials.txt:
Missing the 180 ohm part number. Add: ERA-6AED181V (180 ohm thin resistor).

sca00/sca00_bill_of_materials.txt:
0.2 ohm is thick film, can find alternate?

davidedelvento, 2024-06-16:
https://www.arrow.com/en/products/rl1632r-r200-f/susumu ?
It's only 1% and not better as you might have hoped, but still is thin film and perhaps adequate or at least better than you have already?

gzweigle, 2024-06-16:
Thanks, I will try that resistor.
Closing the issue because checked in parts files with new resistor values and also will test the suggested.

Closed 2024-06-16.

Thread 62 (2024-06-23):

DOC: Using non-resistive pedals

gzweigle, 2024-06-23:
The IPS is setup for passive, resistive pedals.
If using an active pedal and do not want to have the PLS PCB, then do not solder R23, R25, and R28.
This issue is created to change the PLS documentation.

gzweigle, 2024-06-24:
Changes to following:
https://github.com/gzweigle/DIY-Grand-Digital-Piano/blob/main/hardware/releases/ips20/ips20_bill_of_materials_0.txt
https://github.com/stem-piano/stem-piano-g-main/blob/main/documentation/assembly_manual.md
https://github.com/stem-piano/stem-piano-g-main/blob/main/documentation/component_manual.md

Also I added a jumper to the growing list of IPS 2.1 enhancements:
https://github.com/gzweigle/DIY-Grand-Digital-Piano/issues/52

Closed 2024-06-24.

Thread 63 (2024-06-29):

FW: nonlinearity in piano vs test setup

gzweigle, 2024-06-29:
I have made progress improving note-to-note accuracy.
However, a recent test indicated that the sensor nonlinearity correction is better in the offline linear actuator test setup than when installed in the action.
This could have been a test or data collection issue.
Creating an issue so I don't forget to investigate when have time.

gzweigle, 2024-07-07:
Details of calibration including what it can and cannot correct will be covered in the technical paper:
https://github.com/gzweigle/DIY-Grand-Digital-Piano/issues/73

Closed 2024-07-07.

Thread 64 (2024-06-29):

DOC: hammer oscillation modes

gzweigle, 2024-06-29:
While working on velocity algorithm improvements, got sidetracked studying the higher-speed (33Ksps) hammer position samples that are streamed over Ethernet.
Seeing several types of oscillations. This is in addition to the normal hammer motion.
One oscillation category is due to the piano structure vibrating.
The other(s) is(are) still a mystery.
Once finish investigation, document so that offline hammer motion analysis algorithms can compensate.

gzweigle, 2024-07-07:
hammer oscillation mode analysis will be covered in the technical paper:
https://github.com/gzweigle/DIY-Grand-Digital-Piano/issues/73

Closed 2024-07-07.

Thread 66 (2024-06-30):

HW: sca part inconsistence

davidedelvento, 2024-06-30:
The BOM lists `U1` as `REF6025` but kicad lists it as `REF6030`

gzweigle, 2024-07-01:
Good question.
The part comes in variants 2.5V, 3.0V, 3.3V, 4.1V, 4.5V and 5.0V.
Probably when I did the schematic I was thinking 3.0V would work. However, that made VCE across the CNY70 too small.  All my documentation in stem piano repo is for 2.5V.
For your sensors you may be able to use a 3.0V or even 3.3V (check the amp range) as the reference value.  The higher the reference the better for signal.

I added a comment to hardware README files that the bill of materials wins if different than schematic.

davidedelvento, 2024-07-10:
I am not sure I understand the problem of `Vce` becoming too small when using an `U1` which provides a higher voltage.

Assuming that `Vce` is `5V` minus what `U1` provides and comparing Fig.3 of https://www.sparkfun.com/datasheets/Robotics/QR_QRE1113.GR.pdf with Fig.8 of https://www.vishay.com/docs/83751/cny70.pdf it appears indeed that `3.0V` might be marginally better.

But looking at the characteristics tables I don't see any other differences. Given the complexities of asking the vendor to manufacture some boards with one part and some others with another part, I'm tempted to let everyone take the `2.5V` version. Do you think that would be a problem? I guess in the worst case I could try to desolder and replace it if necessary (it would be a painful thing to do, but not impossible, as far as I can tell...)

gzweigle, 2024-07-11:
Yes, for HPS, vdd=3.3 and with vref = 2.5 the difference (vce) is 0.8 volts when hammer is at stop.
If vdd > 3.3, vref can be bigger.
I agree vref=2.5 for all boards is simpler.
Select ACE resistors so the output is 0 to 2.5v as hammer goes from rest to stop.

gzweigle, 2024-07-13:
1. Yes.

Vdd is an input to the HPS. For HPS 0.8, Vdd is the voltage difference between pins 1 and 2 of J0.

The HPS 0.8 is designed to receive 3.3V for Vdd.

2. Yes.

For example, with the resistors in the HPS 0.8 parts list, HPS 0.8 will output a voltage near 0 when the hammer is at rest and a voltage of near 2.5V when the hammer is at the stop bar.

Therefore, I selected REF6025 for the ADC reference since 2.5V matches the maximum output of the HPS 0.8.

3. This one is a little more complicated to answer:

REF6030 will also "work" with HPS 0.8. In this case, when HPS 0.8 is at its maximum output of 2.5V, the ADC will output 2.5/3.0 of full scale.  The full scale of ADC is not used.  This gives up some noise margin.  But the piano will "work".

What didn't work was sizing the resistors on HPS 0.8 so that it outputs 3.0V when hammer is at the stop bar. In this case, the voltage drop across the CNY70 was too small (3.3-3.0).

4. Not sure I understand but if the interest is to use REF6030 for all boards, it will also "work" for the HPS 0.8, with the caveat that these sensors will not use the full range of the ADC.

davidedelvento, 2024-07-14:
Thanks, this is extremely helpful, now I understand everything (and I have been able to run some tests).

I now also understand better why you wanted to put potentiometers in some of these designs. There is a key-to-key variability which (upon inspection and testing) is due to the different reflectivity of the hammers. That, compound with the different brightness that can be achieved with different currents at the LEDs make settling to a definitive answer a bit tricky. The QRE1113 can easily reach 3.05V when energized around 3.3V if the target is "shiny" enough (e.g. white paper, new hammers). On the other hand, a less reflective target (e.g. old hammers, even after filing them to make them very white) can stay easily under 2.5V

Puzzlingly, that maximum value does not change when changing the value of the bias resistor on the phototransistor (the non maximum achieved with a old hammer does). As such, I am tempted to have a 6030 installed -- but I fear they would get confused and ship those to Europe and give me the 6025 instead, so I am settling on the 6025 to begin with and then I will figure out some way of "voicing" the hammers to achieve the maximum range.

Thanks

Closed 2024-07-01.

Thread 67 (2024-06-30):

HW: kicad file for IPS board missing sockets for Teensy

davidedelvento, 2024-06-30:
This is probably historical since earlier to envisioned soldering the Teensy on, but better having sockets.

gzweigle, 2024-07-01:
When I created the schematic for IPS I didn't realize that using a symbol for both Teensy and SCA would later cause problems with specifying the headers. So, instead of redoing the schematic, as a workaround, I had decided to just specify the sockets in the bill of materials:
https://github.com/gzweigle/DIY-Grand-Digital-Piano/blob/main/hardware/releases/ips20/ips20_bill_of_materials_0.txt.
Because of the workaround, I am going to close this issue. Feel free to re-open if the answer isn't sufficient. However, unless this change is a showstopper for creating boards, it will be a very low priority.  I will also add to the IPS 2.1 project to-do.

Closed 2024-07-01.

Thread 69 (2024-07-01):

HW: add KiCad v8 for all boards

gzweigle, 2024-07-01:
Project scope:
- Add KiCad v8 for all existing hardware.
- Keep KiCad v7 as well.
- Specify in repo which boards were built and tested with which KiCad version. This enables optionally making boards based on the version that was fabricated and tested.
- Fix errors and warnings due to KiCad library and other changes.
- Validate schematic changes by first running PCB DRC on existing (v7) PCB vs updated (v8) schematic before updating the PCB to v8.
- Goal: when fabricated, PCB is identical to v7.

gzweigle, 2024-07-05:
All KiCad 8 are now in *_v1 folders.
See
https://github.com/gzweigle/DIY-Grand-Digital-Piano/blob/main/hardware/releases/README.md
for explanation of numbering system (it isn't perfect but its backwards compatible with existing before I realized the KiCad challenges).

Closed 2024-07-05.

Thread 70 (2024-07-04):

HW: ACE board pins incorrectly set up all on the same side

davidedelvento, 2024-07-04:
In KiCad.

A picture is worth 1000 words

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

see how that mismatches the picture of the actual thing which has some things on one side and some on the other

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

gzweigle, 2024-07-04:
I don't know how to tell KiCad 3D Viewer Through-hole model Appearance to put on front or back.
Almost done with KiCad v8 update all circuit boards - if I figure out the 3D viewer appearance setting, will include that too.

davidedelvento, 2024-07-04:
> I don't know how to tell KiCad 3D Viewer Through-hole model Appearance to put on front or back.

Just to be clear that is not a matter of appearance in the 3D viewer, it's matter of fabrication error. As is, everything is placed on the top and nothing on the bottom, and if it is sent to fabrication it will come assembled as in the 3D viewer (i.e. incorrectly).

See the `aceA00-bottom.pos` file for detail:

```
### Footprint positions - created on 2024-07-04T11:35:51-0600 ###
### Printed by KiCad version 8.0.3
## Unit = mm, Angle = deg.
## Side : bottom
# Ref     Val       Package                PosX       PosY       Rot  Side
## End
```

To select the actual placement, go into the properties of the part (shortcut `E` once the part is selected in the GUI) and pick front or back as placement. Let me see if I can make a PR for this.

davidedelvento, 2024-07-04:
I made #71 trying to fix this issue (hopefully I did not cause other trouble....)

davidedelvento, 2024-07-04:
Same problem with the SCA board, attempted fix in PR #72

gzweigle, 2024-07-04:
> Just to be clear that is not a matter of appearance in the 3D viewer, it's matter of fabrication error

Good point. To fix this I am changing the footprint silkscreen so that it is on the bottom of board. For both SCA and ACE circuit boards. And to do that, I am in the process of revising the ACE from 0.0 to 0.1 and the SCA from 0.0 to 0.1.

I will also change the placement instructions as you note above. For consistency with how I am organizing the GitHub files, these revised PCB will be in new subdirectories which I am creating.

Also, FYI to address KiCad 8 issue I am creating new directories under the original PCB directories, and keeping the original with KiCad 7. I want to keep the original KiCad 7 files in the original directories visible (not buried in github history) because those are what were fabricated and tested... so far.

Thanks!

gzweigle, 2024-07-05:
Because this was a visible board change, I incremented the board version number.
https://github.com/gzweigle/DIY-Grand-Digital-Piano/tree/main/hardware/releases/sca01
https://github.com/gzweigle/DIY-Grand-Digital-Piano/tree/main/hardware/releases/aceA01
I also fixed an unrelated label error on ace version 0.0 and removed the ground plane because it doesn't add much value for this board, but it created a large surface for the soldering to heat which made soldering annoying.
I plan to build and test this board to makes sure I didn't break anything.

davidedelvento, 2024-07-05:
> I also fixed an unrelated label error on ace version 0.0 and removed the ground plane because it doesn't add much value for this board

I think the ground plane may add a bit of EMI protection, even though at the frequencies we are dealing with is probably marginal/irrelevant?

gzweigle, 2024-07-05:
Yeah.
Note that the larger SCA and IPS both have ground planes.
For the interposer the runs are very short and the signals relatively slow.
I could make a version (0.2) with the ground plane too if interested.

Closed 2024-07-05.

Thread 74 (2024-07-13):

HW: pedal jack cannot be found

davidedelvento, 2024-07-13:
You wrote "if" in https://github.com/gzweigle/DIY-Grand-Digital-Piano/issues/52#issuecomment-2225571769

Unfortunately, I am unable to find anything suitable and that is stopping progress on https://pianoclack.com/forum/d/1510-diy-electronic-purchase/

Can you please share the part number you used?

gzweigle, 2024-07-13:
Good point that the information in ips20_bill_of_materials_0.txt is not enough.  I will add more details.

Note that I just tried taking the description from the ips20_bill_of_materials_0.txt, and put it into a web search.
"uxcell Audio 6.35mm"
And it returned multiple sources to buy.

davidedelvento, 2024-07-13:
Thanks.

Yes, I did the same search, but unfortunately returned a large number of ebay/amazon/aliexpress results which are not specific product but something without a part number that I could in the order (I did not check them all, but I checked a large number of them and none had a part number). Moreover, many of them had different pin locations which would not match the PCB (as you wrote in that other issue)

I did the same search on Mouser, Digikey etc and that did not return anything. Tweaking the search terms I was able to find something okay (right socket and right number of pins) but none had a footprint compatible with the PCB.

davidedelvento, 2024-07-13:
Maybe this? Not completely clear to me if the footprint is the appropriate one: https://www.mouser.com/ProductDetail/CUI-Devices/SJ-63062A

gzweigle, 2024-07-14:
This in Amazon is it

uxcell 6.35mm 1/4 Inch 3Pin Mono Jack Panel Mount PCB Connectors Metal 6.35mm Headphone Socket Audio Stereo Connector

It is black with red along bottom.

I will put more info in repo too.

davidedelvento, 2024-07-14:
Thanks, but you did not post the link. The first hit is https://www.amazon.com//dp/B00X77SADC/ -- is that the one? It has several bumps in the bottom (probably for slots in the PCB? does it work even if the PCB does not have the slots?)

I will try adding such Amazon part to the order, but given how picky the vendor has been with not exactly part-numbered components (even for pin-headers!!!) I think they will balk at it. In such a case I will order it without and I'll let @AkariProd solder his own ones.

gzweigle, 2024-07-14:
yes that looks right.  Its really easy to solder.

And, yes it works with the slots. Stands the part up off the PCB slightly but the pins are so long they still go through the PCB by a good 1 millimeter.

davidedelvento, 2024-07-14:
Sounds great thanks. As far as I am concerned, this issue could be closed, not closing it myself in case you want to consider including the link in the BOM.

gzweigle, 2024-07-21:
updated documentation

Closed 2024-07-21.

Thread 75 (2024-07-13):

HW: pedal resistors clarification

davidedelvento, 2024-07-13:
The BOM contains the lines

```
R23,    4700 ohms,             0805,       ERA-6AED472V,         No,            0.50,        0.125W. 5% tolerance or better. For pedals. Install if using passive pedals.
R25,    4700 ohms,             0805,       ERA-6AED472V,         No,            0.50,        0.125W. 5% tolerance or better. For pedals. Install if using passive pedals.
R28,    4700 ohms,             0805,       ERA-6AED472V,         No,            0.50,        0.125W. 5% tolerance or better. For pedals. Install if using passive pedals.
```

For the group order of https://pianoclack.com/forum/d/1510-diy-electronic-purchase/ some people plan to use passive pedals and some people plan to use active ones (i.e. just CNY70 or QRE1113 sensors like the hammer ones).

Do I understand correctly that if these resistors are installed the active pedals won't work correctly?

Assuming that is the case, consider that there are `16*6=96=88+8` channels, i.e. 8 more than needed for keys only. Given that the pedals use three channels, would it be possible to use 3 channels for the passive pedals and 3 channels for the active ones (and we still have 2 to spare) and avoid this hardware complication?

gzweigle, 2024-07-13:
Will active pedals use the quarter inch jack inputs?

The reason I ask is because:
The quarter inch jacks connect to header J46 and they don't connect to anything else.
The resistors R23, R25, and R28 connect to the quarter inch jack outputs and these resistors don't connect to anything else.
To use quarter inch jacks, one uses a ribbon cable to connect J46 to one of the 96 inputs along the back of the PCB.

If active pedals connect to one of 96 inputs, and do not use the quarter inch jacks, then:
Install the resistors R23, R25, and R28.
And:
(a) Those using passive pedals use the quarter inch jacks.
(b) Those using active pedals connect directly to any of the 96 inputs along back of PCB.

Will that work?

davidedelvento, 2024-07-13:
No active pedals (at least the ones I have in mind) will use the pins like keys.

What you have designed sounds great and would work great, thanks.

Closing the issue.

Closed 2024-07-13.

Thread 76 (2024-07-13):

HW: Pedal resistors

davidedelvento, 2024-07-13:
This is probably leftover from #54 -- the BOM states 10 Ohm for R22 R26 and R29. But KiCad still has 10 kOhm. I am proceeding assuming that the BOM is correct, but please confirm.

gzweigle, 2024-07-13:
Correct 10 ohms.

davidedelvento, 2024-07-14:
Awesome, thanks. Not closing this issue since you may want to fix the value in KiCad.

gzweigle, 2024-07-21:
Documentation - use bom not schematic so we're good.

Closed 2024-07-21.

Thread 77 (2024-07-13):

HW: fuses

davidedelvento, 2024-07-13:
I understand that fuses are just one level of protection and they might or might not work for the purpose, so with all the obvious disclaimers of not taking you liable for anything, this being all at my risk etc etc, I would like to ask your opinion regarding these options (by the way, I would love for the hold and trip currents to be closer, but they aren't)

* For F1 use a 6V, 3.8A (hold), 8A (trip) fuse such as https://www.digikey.com/en/products/detail/bourns-inc/MF-USML380-2/7394484  and for F2 use a 6V, 1.9A (hold), 5A (trip) fuse such as https://www.digikey.com/en/products/detail/littelfuse-inc/MICROSMD190LR-2/3743342 (by the way all SMT fuses seem to be "obsolete" on digikey)
* For both F1 and F2 use the first option above
* For either or both F1 and F2 use a 0 Ohm resistor instead

gzweigle, 2024-07-14:
I clarified the documentation.
We don't know what power supply people will use.

gzweigle, 2024-07-14:
You could leave them off and have individuals decide based on their system.
Its a fairly large 1210 footprint.
That is the direction I changed the documentation.

gzweigle, 2024-07-27:
Added F2 to parts list
https://github.com/gzweigle/DIY-Grand-Digital-Piano/blob/main/hardware/releases/ips20/ips20_bill_of_materials_0.txt

gzweigle, 2024-07-27:
Also, I made a video on replacing a surface mount fuse and put the link to video in documentation here:
https://github.com/gzweigle/DIY-Grand-Digital-Piano/tree/main/hardware/releases/ips20

Closed 2024-07-27.

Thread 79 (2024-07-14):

DOC: ribbon cable error

gzweigle, 2024-07-14:
Track down a persistent small coupling error on adjacent notes.
It is the ribbon cables.
Update assembly documentation.

gzweigle, 2024-07-14:
Documentation is updated in stem-piano-g repo

davidedelvento, 2024-07-14:
Yeah, ideally the ground and signal cables should be twisted around each other as I described at https://pianoclack.com/forum/d/637-build-your-own-hybrid-piano-step-four-the-cables -- unfortunately that's a pain, but I'm working on building a machine to make that cable-making easier (of course that link is for when I used a different electronics, but still...)

The good news is that there exist pre-twisted cables, which I am still exploring about. The bad news is that it's a niche product with limited options (e.g. length of twisted section, pitch of the cables, etc) which make it hard to adapt to our needs. As I wrote in that page above, one should design the (mechanics of the connectors of the) sensorboards and ADC boards based on cable availability, rather than the other way around... Well, maybe next version.

One example of such cables: https://www.digikey.com/en/products/detail/3m/1700%2F10%2520100/9479266

Closed 2024-07-14.

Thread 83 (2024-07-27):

HW: Option to power the LEDs via external constant current supply

davidedelvento, 2024-07-27:
This is potentially related to #40 and #14 and definitely to https://github.com/gzweigle/DIY-Grand-Digital-Piano/tree/main/hardware/releases/aceA00 as well as https://github.com/davidedelvento/piano-conversion/tree/QRE1113GR-4x-four-holes/hardware/sensorboards/2040-centered-4x-QRE1113GR

In brief: LED output depends on the current that flows into them, regardless of the voltage drop that the LED incurs in. Device-to-device variability, and other factors, make the voltage drop different in different LEDs, which makes a constant-voltage power supply (the one currently used in the design) a bit less stable and a bit more subject to calibration and calibration drifts.

A simple off-the-shelf linear regulator such as the IHB120-0.2 (if one would like to power all the LEDs in a single strip) or lower voltage such as the HB48-0.5-AG (spitting the LEDs in multiple strips, probably better for maintenance) can be used to very stably power a voltage-to-current regulator such as the CL220N5-G which is inexpensive and can be used either for single strip or for multiple strips in parallel as described in its datasheet (Fig 3-5).

This setup would guarantee a more constant LED-to-LED brightness as well as a more stable in time brightness (since the residual ripple is extremely low). Moreover, there is no need for current-limiting resistors, and so if they are left out of the board no power dissipation on them (however the linear voltage supply will have an efficiency of just about 60%, but that is already similar to what is installed on the IPS board).

Of course all of this could be implemented on the IPS itself rather than as an external solution as described here

gzweigle, 2025-04-26:
This is an interesting idea.
Will close because if I decide someday to revisit the sensor design, I will review all historical issues anyway whether open or closed.

Closed 2025-04-26.

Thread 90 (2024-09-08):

HW: discussion related to IPS 2.1

davidedelvento, 2024-09-08:
To avoid making issue #52 a giant discussion, let me discuss here some things which I think you could/should do for the next version

1. mounting holes -- they are too small, and make the IPS board very flimsy, even just mounting is, especially when attaching/detaching cables and other boards. I know one should not do these things too often, but still... I strongly recommend you make the holes at least M3 and ideally M4 size
2. cabling -- in my brief experience so far, the situation is worse than I thought. Perhaps a mitigation strategy could be to use ubiquitous, inexpensive and high quality ethernet cables, rather than ribbon. Each cable such as https://en.wikipedia.org/wiki/Ethernet_over_twisted_pair would carry signal for 4 sensors. I know your current design involves single sensor boards, but I think you should consolidate them in groups of 4, which is extremely convenient for assembly and regulation (we can have that conversation separately). Even if you want to keep the HSP for single sensors, still grouping the signals in an ethernet cables at the IPS would make things much easier (and a split can be easily made near each sensor if you want to leave them unchanged). This is possible with an interposer board, obviously, but I think it would be ideal if made straight on the IPS board, to minimize size, cost and EMI.
3. In issue #52 you wrote

> Quarter inch jack interposer board

4. not sure if you mean the same thing I mean for "interposer". For me that word means a PCB that is placed in between two things, both electrically and (most importantly) physically. Here I think the best solution would be a separate board (or even just panel-mount jacks!) with some cabling (ribbon?) going to the IPS, which would have only header pins. Same for most things, including MIDI, Ethernet (should use twisted pairs, but probably the rate is slow enough that it might not matter), power, etc.
5. Related to this, and perhaps you intend to do that but did not say in the list, I think making the IPS much smaller would be better, both for convenience of installation (it is really hard to find that space inside the cabinet without interfering with other things, even more so when using two of them for the damper sensors) and for cost. In my view the IPS should have headers for the Teensy and the SCA, then the multiplexers, and the headers (ideally ethernet-like jacks) for the sensors. Maybe the switches/buttons/LED, and that's it. Everything else should go with few more headers so that it can be installed in a separate location (particularly the display)
6. You also wrote

> Move CAN connector to back of board.

7. I don't understand this, and I strongly oppose it. Dealing with the board as is, it's already difficult. Having headers on the back of the board too would be a nightmare (but perhaps I misunderstood what you meant by "back" and you did not really meant the other side of the board, just a different location?)
8. I think I had a couple of other things, but I don't recall them now and I think they were minor compared to these ones

gzweigle, 2024-09-09:
(2) - agree, a better solution is needed.  The ACE boards help a little but not sufficiently.

(4), (5) - this would be interesting and very flexible... I will think about it. Maybe it is called IPS 3.0 too. Saves at least 1.5 inches of width.
Note that with present board, future SCA design variations can optionally fill the entire TFT PCB space. I designed it this way after considering the mm^2 required for 6 parallel ADC on a new data acq card. So that is why I was ok with the quarter inch jack real estate.

However, taking the modular concept one step further, I could in theory put each function on its own board.
1 board for 96 analog inputs
1 board for data acq
1 board for processing
1 board for display and switches
1 board for pedals
1 board for data i/o
1 board for display
Connect them together with Ethernet cables (as you noted).
Then, everything is highly modular, incredibly flexible/expandable, and minimally small.

davidedelvento, 2024-09-14:
> Note that with present board, future SCA design variations can optionally fill the entire TFT PCB space. I designed it this way after considering the mm^2 required for 6 parallel ADC on a new data acq card. So that is why I was ok with the quarter inch jack real estate.

Would this be to reduce latency / scanning time? If so, rather than having larger SCA and IPS (which are expensive to make) why not have multiple boards like you currently have for hammer and damper sensors? Most PCB houses have a minimum order of 5 boards anyway, so having more boards smaller rather than one board larger makes financial sense (and ease the logistics of cabling since each board could be attached only on (say) an octave or two. Of course a communication protocol better/faster than the CAN bus might be needed.

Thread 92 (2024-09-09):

SW: compilation error

davidedelvento, 2024-09-09:
```
/home/davide/Arduino/src_hammer/src_hammer.ino: In function 'void setup()':
/home/davide/Arduino/src_hammer/src_hammer.ino:166:7: error: 'class TftDisplay' has no member named 'Clear'
  166 |   Tft.Clear();
      |       ^~~~~

exit status 1

Compilation error: 'class TftDisplay' has no member named 'Clear'
```

fixed by
```
--- a/firmware/releases/ips2_hammer/src_hammer.ino
+++ b/firmware/releases/ips2_hammer/src_hammer.ino
@@ -65,7 +65,9 @@ Switches SwSCA1;
 Switches SwSCA2;
 TestpointLed Tpl;
 Timing Tmg;
+#ifdef TFT_INSTALLED
 TftDisplay Tft;
+#endif

 MIDI_CREATE_INSTANCE(HardwareSerial, Serial1, mi);
 uint8_t Midi_Buffer[MIDI_BUFFER_SIZE];
@@ -97,8 +99,10 @@ void setup(void) {
   if (Set.debug_level >= DEBUG_STATS) {
     Serial.println("Beginning hammer board initialization.");
   }
+#ifdef TFT_INSTALLED
   Tft.Setup(Set.using_display, Set.debug_level);
   Tft.HelloWorld();
+#endif

   // Initialize the nonvolatile memory.
   // Initialize early in case any setup() uses storage.
@@ -163,7 +167,9 @@ void setup(void) {
     Serial.println("Finished hammer board initialization.");
   }
   delay(2000);
+#ifdef TFT_INSTALLED
   Tft.Clear();
+#endif

 }

@@ -300,7 +306,9 @@ void loop() {

     if (Set.test_index < 0) {
       // Run the TFT display.
+#ifdef TFT_INSTALLED
       Tft.Display(switch_tft_display, calibrated_floats, damper_position);
+#endif
     }

     // Debug and display information.
@@ -317,4 +325,4 @@ void loop() {

     Tpl.SetTp8(false);
   }

```

gzweigle, 2024-09-09:
thanks, and I pushed a commit that fixes

Closed 2024-09-09.

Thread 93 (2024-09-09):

FW: How to design a MIDI USB device for piano

gzweigle, 2024-09-09:
Location for tracking research.

davidedelvento, 2024-09-09:
These should provide some related info

* https://forum.pjrc.com/index.php?threads/teensy-4-1-adafruit-tinyusb-support.64627/
* https://forum.arduino.cc/t/library-hell-specifically-tinysub-and-midi-in-general/923078/2

and most importantly

* https://www.pjrc.com/teensy/td_midi.html

I've done this on a RPi Pico v1, which is an extremely limited board, so on the Teensy it should not be that hard...

davidedelvento, 2024-09-15:
Looks like this is super-easy, simply

* in the menu Tools -> USB select MIDI + serial rather than only serial
* in line https://github.com/gzweigle/DIY-Grand-Digital-Piano/blob/main/firmware/releases/StemPianoIPS2/src/midiout.cpp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 just add `usbMIDI.sendNoteOn(midi_note, velocity_potentially_muted, midi_channel_);`
* and equivalently a couple of lines below with `sendNoteOff`

And should work out of the box. I will try asap (hopefully tomorrow), but I thought to let you know beforehand in case you wanted to try it yourself first.

GalhardoLab, 2024-09-15:
a - it is also necessary to find the instances of CC64, 66, 67 for the pedal messages.

b - there are some arduino midi-usb libraries is which it is possible to buffer several midi commands (maybe up to 16, but I have to double check) and dump them all at once with the same timestamp. This is helpful to send together notes that are triggered within the same scan cycle, thus avoiding a slight "broken chord" effect.

b1 - I am not sure if that arduino library is compatible with Teensy, nor if the teensy library is capable of the same...
b2 - I am not sure if this firmware has one master cycle scan, or if it is interrupt-like... If there is no scan cycle, the hold and dump approach does not make sense.

gzweigle, 2024-09-21:
I also edited the documentation.

Closed 2024-09-21.

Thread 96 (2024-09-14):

HW: label inp and gnd on ACE

davidedelvento, 2024-09-14:
Label `gnd` or ground symbol instead of J4 and J9

Label 'inp' instead of J2 and J7

davidedelvento, 2024-09-14:
Or even better label `E` (for emitter) for J2 and J7 and `C` for collector J5 and J10. And now that I see it better, another cabling complication, it would have been better if the rows for E and C were adjacent, as they are it complicates my cable building a lot, I wish I had noticed beforehand.... Maybe for the next version?

gzweigle, 2025-05-04:
Working on damper sensor upgrades and investigated this. The rows match the rows on IPS which helps me keep everything straight.  I will add the idea to swap E and C to the IPS 2.1 list.

gzweigle, 2025-05-17:
> Working on damper sensor upgrades

Sure enough these labels would have been useful.  Adding to an upcoming manufacturing run.

gzweigle, 2025-05-18:
created ACE board version 0.2 with the power, ground, and signal labels.

https://github.com/gzweigle/open-hybrid-piano/tree/main/hardware/releases/aceA02

Closed 2025-05-18.

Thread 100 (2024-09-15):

DOC: make wiring order diagram more prominent

davidedelvento, 2024-09-15:
I was very familiar with https://github.com/stem-piano/stem-piano-g-main/blob/main/documentation/assembly_manual.md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 existence, but I was not sure of one thing so I wanted to check that.

I've spent 10 minutes finding it. I recommend making it more prominent, perhaps with a dedicated section, and for sure with a "Wiring" link in between 3. and 4. at https://github.com/stem-piano/stem-piano-g-main/blob/main/documentation/construction_manual.md

davidedelvento, 2024-09-28:
Related to this and to make the wiring job easier: would it be possible to change the wiring order in firmware and I mean in a random order?

Reason to ask: given the way that the hammers are grouped, it would be incredibly easier if I could (say) connect the IPS keys numbers 0 to 7 to what are piano keys 2 to 9 and then connect IPS8-15 to piano 10-17 and then IPS16-23 to piano 20-27 etc and then using an arbitrary IPS slot to connect the "loose" piano keys that I missed, in this example so far 0,1,18,19.

I am sure this is *possible*, it's just software obviously. The question is if this is possible by introducing a LUT and using it rather than direct assuming things, and if such a change would be small (handful of places) or massive (turn the whole code base upside down).

Assuming it is "small", would you accept a PR for such a change? I want to make my (and other people's) wiring life easier, but I don't want to diverge from your main code base

gzweigle, 2024-09-29:
I can make this change.  Because I can combine it with void SixChannelAnalog00::ReorderAdcValues(unsigned int *);

gzweigle, 2024-09-29:
Code is updated for custom changing wiring order in firmware.
See hammer_settings.cpp and also the commit diffs.
Let me know if this is what you needed.

Also I updated the wiring diagram documentation

Closed 2024-09-29.

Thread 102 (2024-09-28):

HW: alternative power supply

davidedelvento, 2024-09-28:
Would you be interested in knowing more, perhaps in a PR, about my power supply strategy which I sketched at

https://pianoclack.com/forum/d/1621-build-your-own-diy-hybrid-piano-step-six-putting-it-all-together/10

I think that has clear benefits compared to your current one, including

* potentially have only two rather than 3 cables per sensor
* avoid the current limiting resistors (if you still have those in your current design)
* simplify wiring, and assembly, especially for people who want to use USB-MIDI, by removing the need for powering up the IPS separately
* maybe be more stable than your current design (not sure since I have not really studied yours, but I have studied mine :-) )

If you are interested, let me know how is it best for me to share what I have done. If you are not interested, simply close this issue, no offense taken, and if a casual reader cares they will find the link above and will be able to learn from there or contact me separately.

gzweigle, 2024-09-28:
What about putting it here?
https://github.com/stem-piano/sensor-systems

davidedelvento, 2024-09-30:
Sounds great. Let's continue the discussion [there](https://github.com/stem-piano/sensor-systems/pull/2)

Closed 2024-09-30.

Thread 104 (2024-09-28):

Use the same nomenclature in the firmware and in the documentation

davidedelvento, 2024-09-28:
I recommend doing this is for everything, but the thing I am struggling now is these switches:

https://github.com/stem-piano/stem-piano-g-main/blob/cfadfc73181cc4308970d7a02c034dba0a3c4c3f/documentation/users_manual.md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

According to my grep'ing there is no `sca_sw1_position2` nor `FREEZE_CAL_VALUES` anywhere in the firmware, so finding where things are happening is harder than it needs to be.

In particular, I have (and cannot) cabled all the keys yet. I notice many problems with my setup and I now suspect that the root cause of at least some is that I have not run (and cannot) the calibration, because I cannot trigger all keys without having all cables. As such, I wanted to change the code of the freeze the calibration and enable that mode anyway even if not all keys are calibrated, so at least I can proceed. I've performed the switch operation, but the LED remains flashing fast, and nothing changes, so perhaps I have not performed it.... Digging into the code and I am confident that I'll have it solved by the time you read this, but I still think a more consistent nomenclature will help those coming after :slightly_smiling_face:

gzweigle, 2024-09-28:
Good point that the documentation does not match the code names.

I added comments to src_hammer.ino.
The src_damper will be the same but I have not checked that in yet because of other compiler errors.

gzweigle, 2024-09-28:
As for calibration - each note calibrates instantly when it is pressed.  The light flashes fast until all 88 are calibrated. But once a note is pressed once, the note is calibrated.

However, the calibration can also get in the way when debugging.  Because it is adding an additional uncontrolled variable to the debugging process.

Here is an idea when trying to get individual keys working:  you could leave sca_sw1_position2 (FREEZE_CAL_VALUES) permanently on. This disables calibration.

Then, either:

- use the velocity scaling setting value to get the velocity in the correct range.

- or, edit six_channel_analog_00.cpp NormalizeAdcValues() and apply a temporary scaling right at the ADC output.  Apply it to normalized_float[].

Closed 2024-09-29.

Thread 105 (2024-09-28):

SW: Capture all hammers in software?

davidedelvento, 2024-09-28:
Current version (both release and research, as far as I can tell) of `get_hammer_data.py` still assume 12 notes rather than 96. Since you made that nice video, I assume you already have the code and simply have not pushed it yet.

Related to #97

gzweigle, 2024-09-28:
ah, ok I will fix this.

davidedelvento, 2024-10-14:
Guessing from the update to

https://github.com/gzweigle/open-hybrid-piano/blob/main/firmware/releases/StemPianoIPS2/src/network.cpp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

I tried this patch

```
diff --git a/software/releases/ips2_analytics/get_hammer_data.py b/software/releases/ips2_analytics/get_hammer_data.py
index 9f5d3b1..5b8f0bf 100644
--- a/software/releases/ips2_analytics/get_hammer_data.py
+++ b/software/releases/ips2_analytics/get_hammer_data.py
@@ -25,11 +25,10 @@
 # num_received_values must match number of sent values from the piano.

 # Convert encoded integers into original value.
-def convert_to_float(a, b, c):
+def convert_to_float(a, b):
     x  =  int(a)&255
     x |= (int(b)&255)<<8
-    x |= (int(c)&255)<<16
-    y = float(x) / 8388608.0
+    y = float(x) / 32768.0
     if y > 1:
         y -= 2
     return y
@@ -37,14 +36,15 @@ def convert_to_float(a, b, c):
 import socket
 import time

-file_length = 20000
-max_packet_size = 100
-num_received_values = 12
+file_length = 40000
+num_received_values = 88
+max_packet_size = num_received_values * 2
+

 # This computer's IP address. Must match value in Teensy.
-UDP_IP = FILL IN BEFORE RUNNING
+UDP_IP = "10.10.0.11"
 # Port number must match value in Teensy.
-UDP_PORT = FILL IN BEFORE RUNNING
+UDP_PORT = 4097

 client = socket.socket(socket.AF_INET, socket.SOCK_DGRAM)
 client.bind((UDP_IP, UDP_PORT))
@@ -63,7 +63,7 @@ for ind in range(0,file_length):
     # Data is sent as three 8-bit integers. Convert to [-1, ..., 1].
     data_float = []
     for k in range(0,num_received_values):
-      data_float.append(convert_to_float(data[3*k+0], data[3*k+1], data[3*k+2]))
+      data_float.append(convert_to_float(data[2*k+0], data[2*k+1]))

     # Write to file as a row of floats.
     # Write only the single note tested.
```

and a small slice of my data looks like

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

Is my patch or my sensing code to be completely broken?

gzweigle, 2024-10-15:
At first glance your patch looks like it should work.

However, just to be sure, I fixed the code. Tested it.  And, put an output file from my testing into the directory with the corrected code.

I created a new issue in case this one needs to stay open for understanding the output data.  However, if the fixed also resolves that, then I will close this issue.

davidedelvento, 2024-10-19:
An update on this. The code you committed is obviously more complete than my quick patch, but the problem I mentioned in my previous update was due to a bug in my plotting script :rofl: and after I fixed that even my earlier capture show decent data (which I still need to study to optimize capture)

I don't think you need to work more on this issue hence I'm closing it

Closed 2024-10-19.

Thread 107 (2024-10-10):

rename repository

gzweigle, 2024-10-10:
The repository name no longer reflects the path this project took.
From GitHub documentation, I can rename the repo and references to the original (including url) will still work.
Those with repo clones may need to reclone or set url.

gzweigle, 2024-10-12:
The repository will be renamed later today.

gzweigle, 2024-10-12:
The new repository name is open-hybrid-piano.

All references to original name automatically link to the new repository name.

For example, https://github.com/gzweigle/DIY-Grand-Digital-Piano/ now redirects to https://github.com/gzweigle/open-hybrid-piano/

davidedelvento, 2024-10-12:
Didn't you want to move it to stem-piano organization too?

davidedelvento, 2024-10-12:
FWIW, forks were automatically fixed too (and hopefully clones will do that on their own also, but I'll keep an eye for it).

See https://github.com/davidedelvento/DIY-Grand-Digital-Piano/tree/main (I did not do anything myself)

gzweigle, 2024-10-12:
> Didn't you want to move it to stem-piano organization too?

For now I have been putting the detailed documentation in stem-piano, with links back to open-hybrid-piano (new repo name) for source and issues tracking.

stem-piano I think scales better when we get millions of contributors :) but open-hybrid-piano has all the history.

davidedelvento, 2024-10-12:
My understanding was that you can change the "owner" (from yourself to the stem-piano "organization") keeping all the links and all the history, but in any case, either one works just fine for me :)

Closed 2024-10-12.

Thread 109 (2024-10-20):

DOC: how to proceed in debugging sensor data

davidedelvento, 2024-10-20:
With my sensors and my action (which you know are both very different than yours), I have a problem finding the appropriate calibration. I'm not asking for a fish, but to be taught to fish, which I can then make it into a PR for the documentation, so others can benefit too. I'm describing my problem just as an example: I speculate you went through something similar and so the actual question is "what steps would you suggest performing to debug similar issues". I know some people are mulling the option to use the system with different kind of sensors (maybe not even optical ones), so this would greatly help them too.

It feels like I am stuck at a note-on velocity of almost always 16. See for example this MIDI and corresponding ADC capture

```
note_on channel=1 note=24 velocity=16 time=0
note_off channel=1 note=24 velocity=23 time=0

note_on channel=1 note=24 velocity=16 time=0
note_off channel=1 note=24 velocity=50 time=0

note_on channel=1 note=24 velocity=16 time=0
note_off channel=1 note=24 velocity=84 time=0

note_on channel=1 note=24 velocity=16 time=0
note_off channel=1 note=24 velocity=79 time=0
note_off channel=1 note=24 velocity=4 time=0
note_off channel=1 note=24 velocity=0 time=0
note_off channel=1 note=24 velocity=2 time=0

note_on channel=1 note=24 velocity=16 time=0
note_on channel=1 note=24 velocity=34 time=0
note_off channel=1 note=24 velocity=10 time=0
```

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

In this example (which I unfortunately I forgot to separately timestamp on the MIDI capture part, given that real-time MIDI has no inherent timestamps) I had:

* only 5 hammer strikes of which 4 where with a keypress and one was with manual raise of the shank
* note that there are several `note_off` events after the 4th `note_on`. This is likely due to the fact that I grabbed the shank with my fingers and so I moved it in an "unexpected" way
* note that there are 6 `note_on` events, I manually grouped the last two together because that was my "manual" strike in which I did by moving the shank with my finger (no keypress involved), so that may be an actual double-strike. This way I was able to achieve a different-than-16 velocity
* `damper_threshold = 0.22` (otherwise the MIDI channel would be flooded by a continuous stream of `note_off` events)
* `hammer_strike_algorithm = 1`

and the following problems:

* velocity is stuck at always 16, regardless of how I make a keypress from ppp to fff
* with manual shank movement (even a relatively slow one, definitely slower than what a keypress achieves) I can get faster velocities, and occasionally a zero (which is different than `note_off` as far as I understand the code in the firmware)
* there are many more peaks in the data captured from the ADC than there are `note_on` events. This is really puzzling. I mean, the ADC values may be too noisy for a gazillion of reasons, so in itself is somewhat okay. But then how can the code correctly identify the moments (if not the velocity) if the hammer strikes??!

I speculate that the hammers move too fast (my sensors are right under the felt, as compared to yours near the flange) and therefore something in the code is too slow to keep pace and measure them fast enough for sensing velocities faster than MIDI 16. Perhaps something else (e.g. some integer conversion) forces the velocity to not be slower than 16 either (given the range of ADC measurements), and so it's stuck there.... unless I move an hammer with my hand, which is slower enough to be measured and hence other velocity values are generated. Pure speculation here, which I could confirm if there is a quick debug setting somewhere to stop the multiplexing and go "full throttle" on one note only. Is there such an option?

Probably confirming the speculation above, but I tried changing various constants with `_scaling` and `_threshold` and the algorithm (`0` or `1`). None of those changes modified anything with regard to this behavior.

gzweigle, 2024-10-20:
I always debugged with calibration off.  One less variable.

Here is some data that could help.  I moved a sensor to be over the hammer.

Attached is:

(1) A picture of the test setup.

(2) Measured values (received over Ethernet) for a very slow (manual move hammer), slow (keypress), and fast (keypress) hammer strike.

(3) A picture of plot of position and velocity.

Observations:

(A) The sensor does not pick up the hammer until it is close to the sensor. So the hammer position data is very nonlinear.

(B) There are less samples due to the faster motion (traveling 40mm at hammer vs 5 mm at flange).  But back-of-the-envelope and looking at this attached data, the 300us sample rate may be ok.

(C) The velocity in attached plot is about 2X for the fast strike compared to the slow strike.  This quick test didn't test if I actually played with 2X the velocity.

[a0_fast_strike.txt](https://github.com/user-attachments/files/17448235/a0_fast_strike.txt)
[a0_manual.txt](https://github.com/user-attachments/files/17448236/a0_manual.txt)
[a0_slow_strike.txt](https://github.com/user-attachments/files/17448237/a0_slow_strike.txt)

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

gzweigle, 2024-10-20:
The results I just shared is with calibration off.

gzweigle, 2024-10-20:
Octave code to recreate my plots.  The zeros in the filter are just to smooth things out.  They aren't necessary.

clear;

x_slow = load("a0_slow_strike.txt");
x_fast = load("a0_fast_strike.txt");

v_slow = filter([1 0 0 0 0 0 0 0 -1],[1],x_slow);
v_fast = filter([1 0 0 0 0 0 0 0 -1],[1],x_fast);

t = [0:length(x_slow)-1]*300e-6;

figure(1);
subplot(2,2,1);
plot(t, x_slow);
grid;
title('position, slow');
xlabel('seconds');

subplot(2,2,3);
plot(t, x_fast);
grid;
title('position, fast');
xlabel('seconds');

subplot(2,2,2);
plot(t, v_slow, 'k', t, v_slow, 'ok');
grid;
title('velocity, slow');
xlabel('seconds');

subplot(2,2,4);
plot(t, v_fast, 'k', t, v_fast, 'ok');
grid;
title('velocity, fast');
xlabel('seconds');

gzweigle, 2024-10-20:
With respect to my observation (B) and this comment in op - "...something in the code is too slow to keep pace and measure them fast enough..."
After thinking about it.
At both hammer and flange, the motion start time and end time are the same.  All that differs is a numerical value.  Therefore, the 300us sample rate is ok for both.  In other words, the "code speed" is ok for measuring at hammer.  The problem is somewhere else.

gzweigle, 2024-10-20:
OK, I was able to get the piano to work, using the test setup (picture in previous comment) with sensor over hammer.

The hammer travels approximately 40mm. The CNY70 and QRE1113 cover a 10X collector current range starting at approximately 5 - 7 mm. This is from my understanding of the datasheets.

Here are the new settings values (hammer_settings.cpp file):

I changed the hammer algorithm to threshold. Maybe not required. But simplified getting it to work.
hammer_strike_algorithm = 1;

Then, I moved the threshold down significantly. Because of the 40 mm vs "5 mm" ranges.
strike_threshold = 0.7;

Also, changed the velocity scaling to a smaller value. This is because of the large nonlinearity when the hammer "comes into view" of the sensor:
velocity_scale = 0.10;

To get the note to sustain, I had to set the threshold quite small, because the catch position is outside the sensor normal range.
damper_threshold = 0.06;

I used the Ethernet streamed data to help me set the above values.

Here is the results for playing A0 soft and loud:

MIDI note (21) index (0) velocity (90) is now ON.
MIDI note (21) index (0) velocity (0) is now OFF.
MIDI note (21) index (0) velocity (66) is now ON.
MIDI note (21) index (0) velocity (0) is now OFF.
MIDI note (21) index (0) velocity (78) is now ON.
MIDI note (21) index (0) velocity (0) is now OFF.
MIDI note (21) index (0) velocity (50) is now ON.
MIDI note (21) index (0) velocity (0) is now OFF.
MIDI note (21) index (0) velocity (97) is now ON.
MIDI note (21) index (0) velocity (0) is now OFF.
MIDI note (21) index (0) velocity (107) is now ON.
MIDI note (21) index (0) velocity (0) is now OFF.
MIDI note (21) index (0) velocity (23) is now ON.
MIDI note (21) index (0) velocity (0) is now OFF.

The white sticker does not want to stay on the felt hammer! That was the biggest problem.
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
davidedelvento, 2024-10-20:
Thanks again!

That noise is indeed at 60Hz, so it must be coming somewhere from the AC distribution frequency. I tried a few other things, including routing the AC power supply elsewhere (as I wrote, this is already with lights off and inside an enclosure, so the only possible luminal noise would be the LEDs on the IPS). I also wired one octave using the Ethernet cables for most of the distance (of course there were still short jumpers, but I twisted them), and the noise remained the same. Here is a close-up

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

The waveform of this noise is peculiar and I think that is telling me something, so I did the FFT and it's telling me (as obvious from the time domain plot too) that there are many other frequencies, but most importantly (which was not obvious from the time domain plot) that the vast majority of the noise is coming from the harmonics of the 60Hz

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

Cleaning up the FFT spectrum removing everything under `2e-5` and performing the inverse creates almost exactly the noise from the time domain, so there is nothing else. I guess the next thing I will try is to battery power the LEDs so I can distinguish LED noise vs sensor/ADC noise (I could do that with an oscilloscope, but I don't have a portable one and the instrument is in a cabinet in a bedroom, so batteries are more practical)

gzweigle, 2025-05-04:
Did this get resolved?
If so, we can close the issue.

davidedelvento, 2025-05-04:
Did it get resolved? Yes, maybe and no.

Yes: if I power everything from batteries, this problem is gone.
Maybe: if I power everything from an excellent power source (e.g. a linear power supply), I can probably still see this issue, but I need to look pretty hard to find it.
No: if I power the LEDs from an excellent linear power supply and the rest of the board from the USB, the problem is still there. Among the ones I have tried, some computers have really bad spectrum (e.g. cheap, old, laptop), and some others are decent (but I would not call them acceptable, e.g. old iMac).

So in conclusion, I think you should do either (or both) of the following:

* mention this problem somewhere in the documentation, warning people to use the best power supply they can afford (and avoid USB-powering at all costs, which I know at least two other people on pianoclack are instead interested in exploring)
* see if you can change anything in the power circuit (of the digital) to make this problem moot. The easy/obvious way would be to add some large capacitor to make a low pass filter. Depending on the power draw that might or might not be practical, I'll leave it to you to check what is the case -- taking also in mind that large electrolytic capacitors have a finite lifespan which may cause problems down the road...

Feel free to close it if you plan to do no action, or to keep it open as a reminder

gzweigle, 2025-05-04:
Interesting...

During earlier development I would often run the piano with USB power. Although never with all 88 keys (only with a subset of sensors, that USB could handle without exceeding its limit).

For example, note here the power input isn't soldered, only USB.
https://youtu.be/DxdRO3M7cgg?t=227

For reference, here is the existing power supply documentation:
https://github.com/stem-piano/stem-piano-g-main/blob/main/documentation/component_manual.md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
I could put the warning in this section.

gzweigle, 2025-05-04:
Added documentation at link above on power supply noise.
Also noted what power supply conditioning is presently on the PCBs, for example the LDOs.

Closed 2025-05-04.

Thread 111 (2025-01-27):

Main board fails to initialize if pedals are in some circumstances

davidedelvento, 2025-01-27:
I finally managed to wire the pedals (which given the geometry of my setup was very challenging). For all three pedals, I am using https://www.sparkfun.com/sparkfun-line-sensor-breakout-qre1113-analog.html as pedal sensor.

I have all three pedals connected to the main board, the board does not initialize, does not present itself over USB-MIDI and does not even connect to Ethernet. If I disconnect two pedals and leave just one, it still behaves in this anomalous way.

However, in the single pedal case ONLY, the main board behaves correctly if before starting the boot, I keep the pedal down (which mean keeping the distance from the sensor high). I cannot reproduce this correct behavior with two or three pedals connected, regardless of how I keep the pedals during the boot.

I am sure there must be something wrong with either my wiring or my sensors, but I think that this can still be considered a firmware bug since even with incorrect data coming from the sensors the board should boot correctly (and help me debug what is wrong, ideally, e.g. by dumping over ethernet the wrong values of the pedals), hence I'm reporting this here.

As a side note, from this behavior, do you have any clue about what might be wrong?

gzweigle, 2025-01-27:
You may want to try putting a

Serial.println("got here");

after each function call in setup()

(and loop() if the code completes setup() ok).

To find where the code hangs.

gzweigle, 2025-01-27:
Also, here is what I put in the help file for similar symptoms.  May give ideas for places to look:

https://github.com/stem-piano/stem-piano-top/blob/main/HELP.md#the-piano-does-not-work-at-all

gzweigle, 2025-04-26:
Close based on adding further help as described above.
Can reopen if issue persists.

Closed 2025-04-26.

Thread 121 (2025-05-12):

FW: damper board mysteriously can cause notes to not play

gzweigle, 2025-05-12:
This was a fun bug to track down.
When the damper board is connected sometimes notes do not play.

The problem is with the optional auto-mute function.
The auto-mute will mute all notes if it detects too many notes at max velocity.
Just in case of a firmware bug it prevents a loud sound.

The bug is caused by checking for max velocity also on the damper release velocity.
This could happen under normal conditions depending on how damper velocity is computed.
But it will never cause too loud of a sound (unlike forte fortissimo of hammer).

Fix by running auto-mute only for hammer velocity.

gzweigle, 2025-05-12:
pushed fix

Closed 2025-05-12.

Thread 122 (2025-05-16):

FW: incorrect short sustain

gzweigle, 2025-05-16:
Very infrequently sometimes a note does not sustain while the key is pressed.

gzweigle, 2025-05-16:
When quantizing damper positions for sending over CAN bus to hammer PCB, if the damper position is exactly 1.0 then it got truncated to a value of 0x00.  Hammer position after normalization should be [-1.0, ..., 1.0].  I didn't notice the corner case for value of 1.0.

The rarely happened because a value of 1.0 is uncommon.  For example 0.99 works fine!

The hammer and damper processing code interpreted a value of 0x00 as damper at virtual strings when actually it was damper maximally far from a virtual piano string.

Fix with a logic test for large and small values instead of a logical AND of bits.

Closed 2025-05-16.

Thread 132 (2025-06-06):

FW: yet another accuracy research

gzweigle, 2025-06-06:
When playing piano, still not 100% happy with the accuracy.

Also discussed here:
https://github.com/gzweigle/open-hybrid-piano/issues/14
https://github.com/gzweigle/open-hybrid-piano/issues/55
https://github.com/gzweigle/open-hybrid-piano/issues/63

And here:
https://www.youtube.com/watch?v=TemXGmkoc-g
https://www.youtube.com/watch?v=yqkRKSGX6kw

davidedelvento, 2025-06-22:
Thanks for sharing. Have you redone the mechanical structure of the sensors as you suggested you were doing in one of your updates?

I think using the cheap L extrusions from hardware store is one (major?) source of your problems since they are not rigid enough and prone to bending and vibrating, let alone being accurate in the initial position. I think 4040 extrusions (like the ones I am using) are a solution to this part of the problem.

Also, having your sensors on the shank, IMHO complicates the matters since there is possibly a note-to-note variation and calibration needed. I think my design of having the sensors on the hammers, with a set spacer with a small hole dramatically improves this problem too, since now each note is exactly sensed then the hammer hits the spacer and the sensor notice it from the small hole (remember, I use small sensors, not the huge CNY70).

I will still have a problem with possibly different reflectivity from note to note, due to difference in hammer felt, but I think I can solve that by filing, which is pretty easy to do (even if a bit messy, but my design allows removal of the action from the cabinet, so the electronics is not affect by that).

To be completely open, none of these are my inventions, I've just taken them from Jay, like I took the electronics and firmware from you. Since you're going faster than I (I'm still stuck at cabling) I wonder if you tested these other options and reached any conclusions.

gzweigle, 2025-06-22:
Thanks. Cool to see a different approaches in the works.

One of my design requirements is sampled position measurements, hammer and damper. So I need the sensed surface to stay less than 8 - 10 millimeters from the sensor. And closer than that is better. Hence shank.

For accuracy, I am working on an optional plug-in addition (to existing hardware system) reference the digital calibration algorithms.

My goal went from "make an open source hybrid piano that works", to "make an open source hybrid piano with high precision and accuracy".

gzweigle, 2025-06-28:
Here is a writeup.

It seems to work. Will make a video when get time someday.

https://github.com/gzweigle/hybrid-piano-calibration/tree/main/pdps

gzweigle, 2025-06-28:
Some browsers are better than others at displaying the equations and equation numbers in document linked above.

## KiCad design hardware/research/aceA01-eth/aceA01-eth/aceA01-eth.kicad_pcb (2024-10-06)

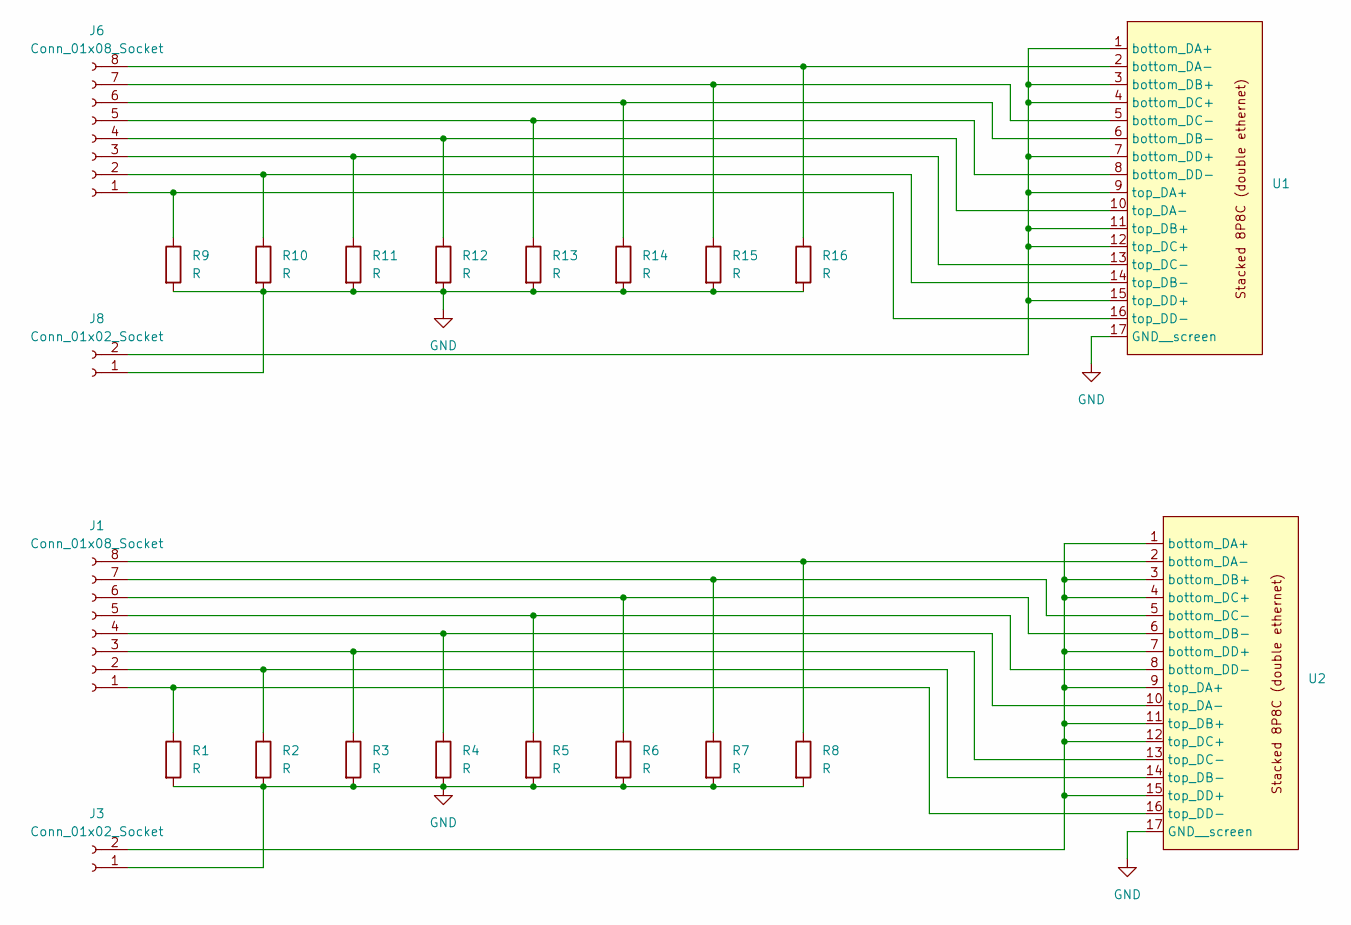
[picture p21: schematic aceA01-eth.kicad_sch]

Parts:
J1: Conn_01x08_Socket; PinSocket_1x08_P2.54mm_Vertical
J3, J8: Conn_01x02_Socket; PinSocket_1x02_P2.54mm_Vertical_SMD_Pin1Right
J6: Conn_01x08_Socket; PinSocket_1x08_P2.54mm_Vertical_SMD_Pin1Left
R1, R2, R3, R4, R5, R6, R7, R8, R9, R10, R11, R12, R13, R14, R15, R16: R; R_0805_2012_1.20x1.40mm_medpad
U1: Stacked8P8C_noFrontPins
U2: Stacked8P8C

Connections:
GND: J3.1, J8.1, R1.2, R2.2, R3.2, R4.2, R5.2, R6.2, R7.2, R8.2, R9.2, R10.2, R11.2, R12.2, R13.2, R14.2, R15.2, R16.2, U1.17 (GND__screen), U2.17 (GND__screen)
unnamed: J1.1, R1.1, U2.16 (top_DD-)
unnamed: J1.2, R2.1, U2.14 (top_DB-)
unnamed: J1.3, R3.1, U2.13 (top_DC-)
unnamed: J1.4, R4.1, U2.10 (top_DA-)
unnamed: J1.5, R5.1, U2.8 (bottom_DD-)
unnamed: J1.6, R6.1, U2.6 (bottom_DB-)
unnamed: J1.7, R7.1, U2.5 (bottom_DC-)
unnamed: J1.8, R8.1, U2.2 (bottom_DA-)
unnamed: J3.2, U2.1 (bottom_DA+), U2.3 (bottom_DB+), U2.4 (bottom_DC+), U2.7 (bottom_DD+), U2.9 (top_DA+), U2.11 (top_DB+), U2.12 (top_DC+), U2.15 (top_DD+)
unnamed: J6.1, R9.1, U1.16 (top_DD-)
unnamed: J6.2, R10.1, U1.14 (top_DB-)
unnamed: J6.3, R11.1, U1.13 (top_DC-)
unnamed: J6.4, R12.1, U1.10 (top_DA-)
unnamed: J6.5, R13.1, U1.8 (bottom_DD-)
unnamed: J6.6, R14.1, U1.6 (bottom_DB-)
unnamed: J6.7, R15.1, U1.5 (bottom_DC-)
unnamed: J6.8, R16.1, U1.2 (bottom_DA-)
unnamed: J8.2, U1.1 (bottom_DA+), U1.3 (bottom_DB+), U1.4 (bottom_DC+), U1.7 (bottom_DD+), U1.9 (top_DA+), U1.11 (top_DB+), U1.12 (top_DC+), U1.15 (top_DD+)

Board: 2 copper layers, 22 parts (20 on the bottom side), 19 nets, no tracks yet.

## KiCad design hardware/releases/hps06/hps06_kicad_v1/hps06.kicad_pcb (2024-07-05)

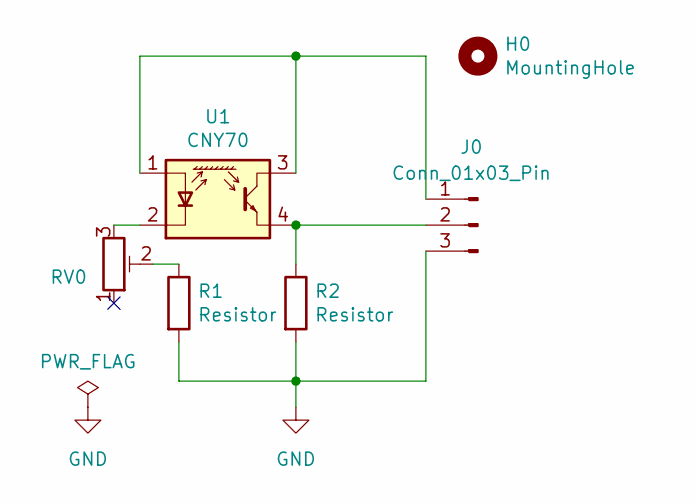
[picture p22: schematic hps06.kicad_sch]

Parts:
H0: MountingHole; MountingHole_3.5mm_Pad_TopBottom
J0: Conn_01x03_Pin; PinHeader_1x03_P2.54mm_Vertical
R1, R2: Resistor; R_0805_2012_1.20x1.40mm_bigpad
RV0: R_Potentiometer_Trim; Bourns_3224X_Vertical_bigpads
U1: CNY70; Vishay_CNY70

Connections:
GND: J0.3, R1.2, R2.2
unnamed: J0.1, U1.1 (A), U1.3 (C)
unnamed: J0.2, R2.1, U1.4 (E)
unnamed: R1.1, RV0.2
unnamed: RV0.3, U1.2 (K)

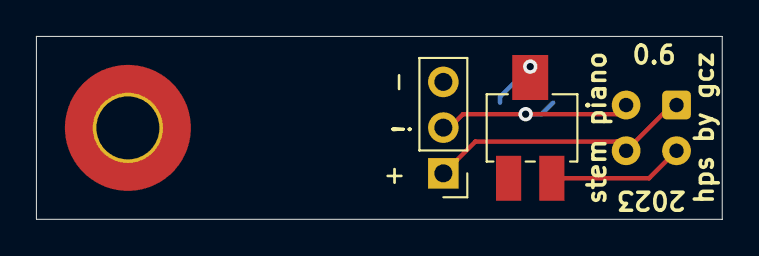
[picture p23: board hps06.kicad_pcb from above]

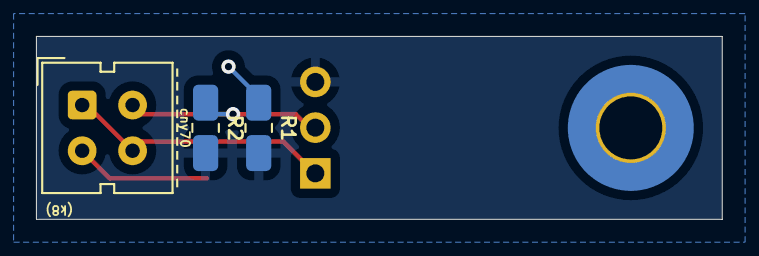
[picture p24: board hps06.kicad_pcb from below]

Board: 2 copper layers, 38.1 x 10.2 mm, 6 parts (3 on the bottom side), 5 nets.

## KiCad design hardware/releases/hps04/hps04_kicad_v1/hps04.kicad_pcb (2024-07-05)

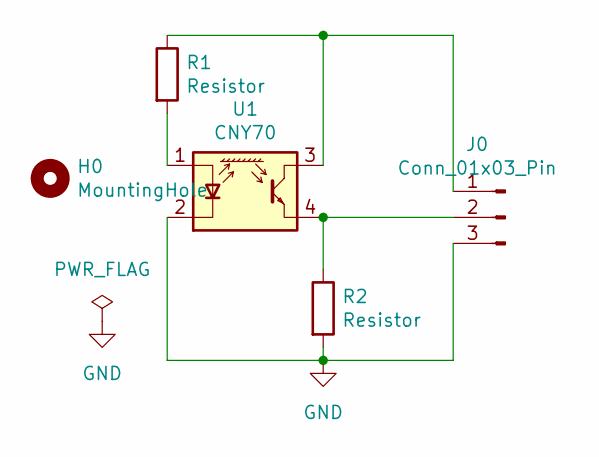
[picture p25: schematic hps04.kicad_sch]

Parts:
H0: MountingHole; MountingHole_3.5mm_Pad_TopBottom
J0: Conn_01x03_Pin; PinHeader_1x03_P2.54mm_Vertical
R1, R2: Resistor; R_Axial_DIN0204_L3.6mm_D1.6mm_P7.62mm_Horizontal
U1: CNY70; Vishay_CNY70

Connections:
GND: J0.3, R2.2, U1.2 (K)
unnamed: J0.1, R1.1, U1.3 (C)
unnamed: J0.2, R2.1, U1.4 (E)
unnamed: R1.2, U1.1 (A)

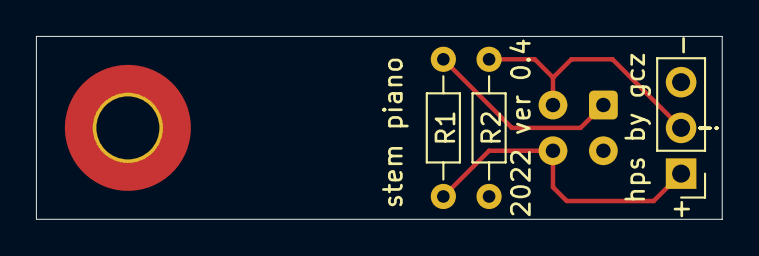
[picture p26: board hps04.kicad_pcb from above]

Board: 2 copper layers, 38.1 x 10.2 mm, 5 parts (1 on the bottom side), 4 nets.

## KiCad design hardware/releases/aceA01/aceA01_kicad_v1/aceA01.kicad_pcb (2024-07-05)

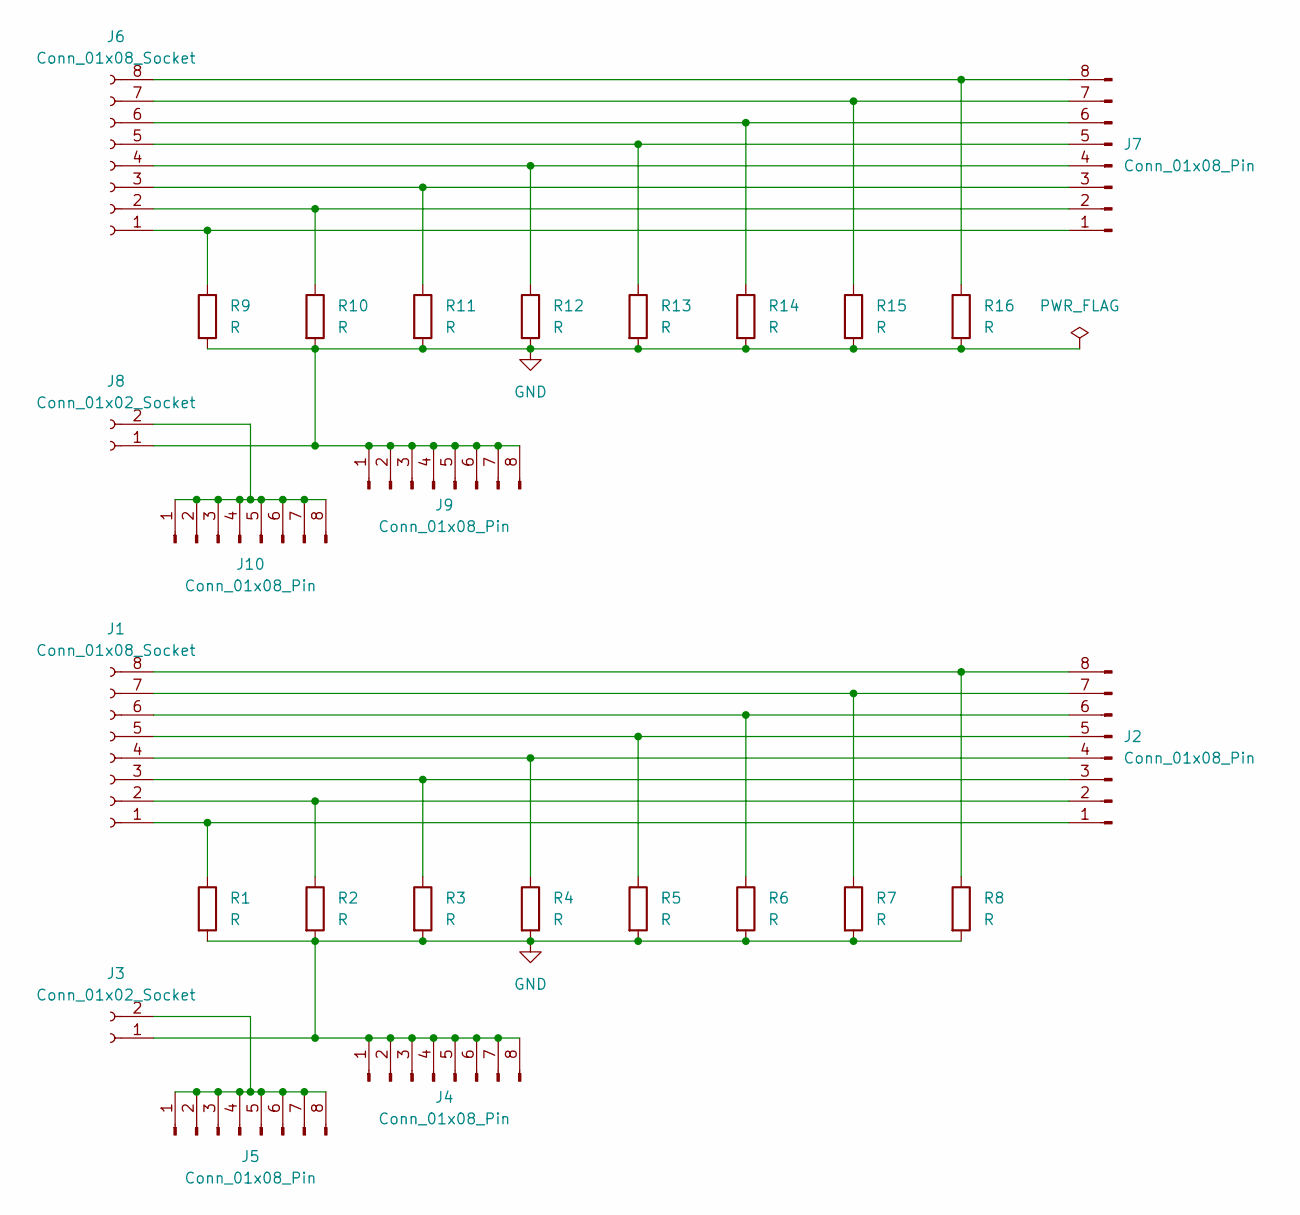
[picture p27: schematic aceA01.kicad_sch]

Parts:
J1, J6: Conn_01x08_Socket; PinSocket_1x08_P2.54mm_Vertical
J2, J4, J5, J7, J9, J10: Conn_01x08_Pin; PinHeader_1x08_P2.54mm_Vertical
J3, J8: Conn_01x02_Socket; PinSocket_1x02_P2.54mm_Vertical
R1, R2, R3, R4, R5, R6, R7, R8, R9, R10, R11, R12, R13, R14, R15, R16: R; R_0805_2012_1.20x1.40mm_medpad

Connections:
GND: J3.1, J4.1, J4.2, J4.3, J4.4, J4.5, J4.6, J4.7, J4.8, J8.1, J9.1, J9.2, J9.3, J9.4, J9.5, J9.6, J9.7, J9.8, R1.2, R2.2, R3.2, R4.2, R5.2, R6.2, R7.2, R8.2, R9.2, R10.2, R11.2, R12.2, R13.2, R14.2, R15.2, R16.2
unnamed: J1.1, J2.1, R1.1
unnamed: J1.2, J2.2, R2.1
unnamed: J1.3, J2.3, R3.1
unnamed: J1.4, J2.4, R4.1
unnamed: J1.5, J2.5, R5.1
unnamed: J1.6, J2.6, R6.1
unnamed: J1.7, J2.7, R7.1
unnamed: J1.8, J2.8, R8.1
unnamed: J3.2, J5.1, J5.2, J5.3, J5.4, J5.5, J5.6, J5.7, J5.8
unnamed: J6.1, J7.1, R9.1
unnamed: J6.2, J7.2, R10.1
unnamed: J6.3, J7.3, R11.1
unnamed: J6.4, J7.4, R12.1
unnamed: J6.5, J7.5, R13.1
unnamed: J6.6, J7.6, R14.1
unnamed: J6.7, J7.7, R15.1
unnamed: J6.8, J7.8, R16.1
unnamed: J8.2, J10.1, J10.2, J10.3, J10.4, J10.5, J10.6, J10.7, J10.8

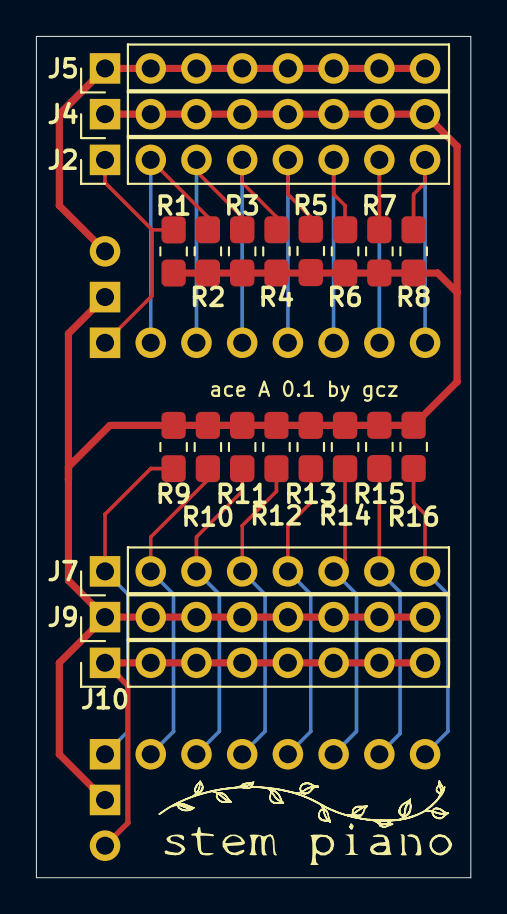
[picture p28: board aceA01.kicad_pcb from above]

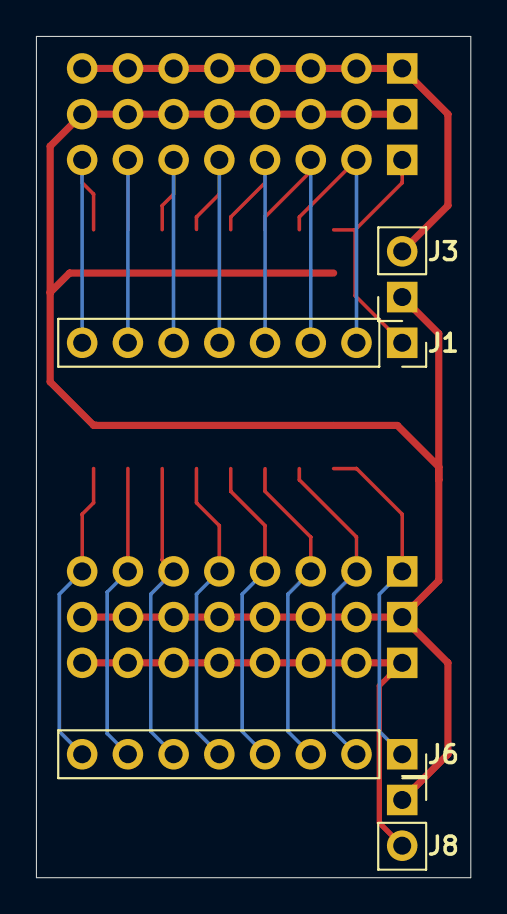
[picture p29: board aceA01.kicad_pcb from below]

Board: 2 copper layers, 24.1 x 46.7 mm, 26 parts (4 on the bottom side), 19 nets.

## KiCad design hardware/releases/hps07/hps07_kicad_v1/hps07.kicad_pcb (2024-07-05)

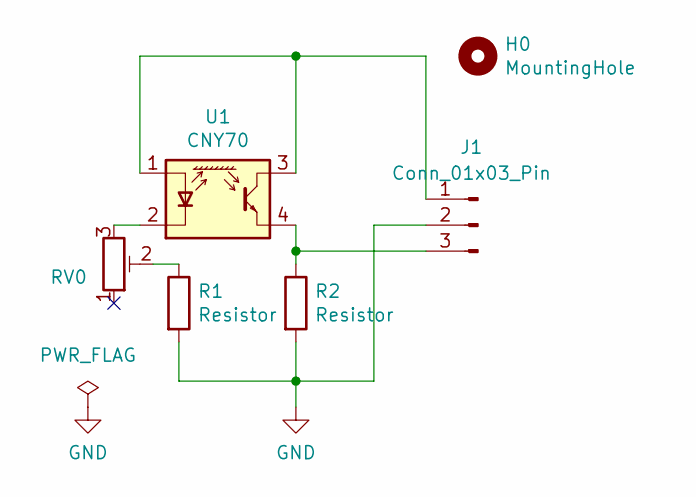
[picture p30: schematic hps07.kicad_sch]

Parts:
H0: MountingHole; MountingHole_3.5mm_Pad_TopBottom
J1: Conn_01x03_Pin; PinHeader_1x03_P2.54mm_Vertical
R1, R2: Resistor; R_0805_2012_1.20x1.40mm_bigpad
RV0: R_Potentiometer_Trim; Bourns_3224X_Vertical_bigpads
U1: CNY70; Vishay_CNY70

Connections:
GND: J1.2, R1.2, R2.2
unnamed: J1.1, U1.1 (A), U1.3 (C)
unnamed: J1.3, R2.1, U1.4 (E)
unnamed: R1.1, RV0.2
unnamed: RV0.3, U1.2 (K)

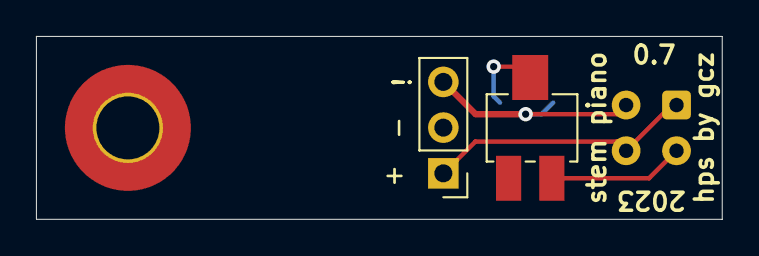
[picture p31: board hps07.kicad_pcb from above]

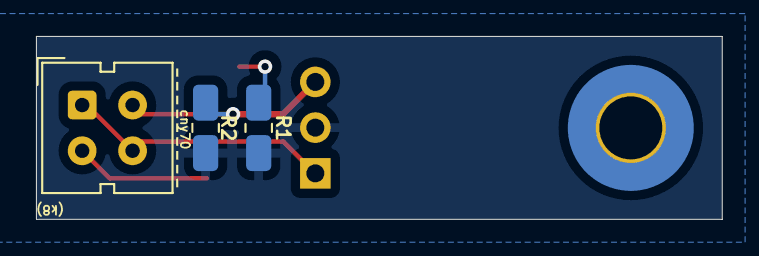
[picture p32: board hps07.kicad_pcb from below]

Board: 2 copper layers, 38.1 x 10.2 mm, 6 parts (3 on the bottom side), 5 nets.

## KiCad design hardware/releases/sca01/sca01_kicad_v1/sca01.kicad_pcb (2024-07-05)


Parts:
C1, C5: 10uF; C_0805_2012_1.18x1.45mm_medpad
C2, C3, C6, C7, C9: 1uF; C_0805_2012_1.18x1.45mm_medpad
C4: 47uF; C_0805_2012_1.18x1.45mm_medpad
C8: 500pF; C_0805_2012_1.18x1.45mm_medpad
H1: MountingHole; MountingHole_2.2mm_M2_DIN965_Pad_TopBottom
J1: Conn_01x13_Pin; PinHeader_1x13_P2.54mm_Vertical
J2, J4: Conn_01x03_Pin; PinHeader_1x03_P2.54mm_Vertical
J3: Conn_01x06_Pin; PinHeader_1x06_P2.54mm_Vertical
J5, J6: Conn_01x01_Pin; PinHeader_1x01_P2.54mm_Vertical
R1: 120K; R_0805_2012_1.20x1.40mm_medpad
R2: small; R_0805_2012_1.20x1.40mm_medpad
R3, R4: 50; R_0805_2012_1.20x1.40mm_medpad
SW1, SW2: SW_DIP_x02; SW_DIP_SPSTx02_Slide_medpad
TP1: analog; TestPoint_Keystone_5000-5004_Miniature
TP2: a; TestPoint_Keystone_5000-5004_Miniature
TP3: sclk; TestPoint_Keystone_5000-5004_Miniature
TP4: dout; TestPoint_Keystone_5000-5004_Miniature
TP5: convst; TestPoint_Keystone_5000-5004_Miniature
TP6: b; TestPoint_Keystone_5000-5004_Miniature
TP7: c; TestPoint_Keystone_5000-5004_Miniature
U1: REF60XX; VSSOP-8_3.0x3.0mm_P0.65mm_medpads
U2: ADS8881; VSSOP-10_medpad
U3: SN74LV4051; SOIC-16_3.9x9.9mm_P1.27mm_medpad
U4: THS4281; SOT-23-5_medpad

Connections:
GND: C1.2, C2.2, C3.1, C4.1, C5.2, C6.1, C7.2, C9.1, J1.10, J4.3, R1.1, R4.2, SW1.3, SW1.4, SW2.3, SW2.4, U1.7 (GND_F), U1.8 (GND_S), U2.5 (GDN), U3.1 (Y4), U3.2 (Y6), U3.6 (INH), U3.7 (GND), U3.8 (GND), U4.2 (V-)
unnamed: C4.2, R2.1
unnamed: J1.4, SW1.1
unnamed: J1.5, SW1.2
unnamed: J1.6, SW2.1
unnamed: J1.7, SW2.2
unnamed: J1.9, TP5.1, U2.6 (CONVST)
unnamed: J1.11, TP4.1, U2.7 (DOUT)
unnamed: J1.12, TP3.1, U2.8 (SCLK)
unnamed: J1.13, U2.9 (DIN)
unnamed: J2.1, TP2.1, U3.11 (A)
unnamed: J2.2, TP6.1, U3.10 (B)
unnamed: J2.3, TP7.1, U3.9 (C)
unnamed: J3.1, U3.5 (Y5)
unnamed: J3.2, U3.4 (Y7)
unnamed: J3.3, U3.12 (Y3)
unnamed: J3.4, U3.13 (Y0)
unnamed: J3.5, U3.14 (Y1)
unnamed: J3.6, U3.15 (Y2)
unnamed: C5.1, C6.2, C7.1, C9.2, J4.1, U2.2 (AVDD), U2.10 (DVDD), U3.16 (VCC), U4.5 (V+)
unnamed: C1.1, C2.1, J4.2, U1.1 (VIN), U1.2 (EN)
unnamed: C3.2, U1.4 (FLT)
unnamed: R2.2, U1.5 (OUT_S), U1.6 (OUT_F), U2.1 (REF)
unnamed: R1.2, U1.3 (SS)
unnamed: C8.1, R4.1, U2.4 (AINN)
unnamed: C8.2, R3.2, U2.3 (AINP)
unnamed: U3.3 (COM), U4.3 (IN+)
unnamed: R3.1, TP1.1, U4.1 (OUT), U4.4 (IN-)



Board: 2 copper layers, 91.4 x 33.0 mm, 33 parts (6 on the bottom side), 28 nets.

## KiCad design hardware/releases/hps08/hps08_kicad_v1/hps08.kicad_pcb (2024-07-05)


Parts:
H0: MountingHole; MountingHole_3.5mm_Pad_TopBottom
J0: Conn_01x03_Pin; PinHeader_1x03_P2.54mm_Vertical
R1, R2: Resistor; R_0805_2012_1.20x1.40mm_medpad
U1: CNY70; Vishay_CNY70

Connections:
GND: J0.2, R1.2, R2.2
unnamed: J0.1, U1.1 (A), U1.3 (C)
unnamed: J0.3, R2.1, U1.4 (E)
unnamed: R1.1, U1.2 (K)


Board: 2 copper layers, 38.1 x 10.2 mm, 5 parts (1 on the bottom side), 4 nets.

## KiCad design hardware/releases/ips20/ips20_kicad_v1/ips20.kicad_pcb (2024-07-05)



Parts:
C1, C2, C4, C5, C6, C7, C8, C9, C10, C11, C12, C13, C14: 1uF; C_0805_2012_1.18x1.45mm_medpad
C3: 0.1uF; C_0805_2012_1.18x1.45mm_medpad
D1, D2, D3, D4, D5, D6, D7: LED; LED_0805_2012_1.18x1.45mm_medpad2
F1, F2: Fuse; fp1210_3225_1.30x2.65mm_medpad
H1, H2, H3, H4, H5: MountingHole; MountingHole_2.2mm_M2_DIN965_Pad_TopBottom
J1: BarrelJack5V; BarrelJack_Horizontal_correct_edge
J2: Cetus_J1B1211CCD; RJ45_Cetus_J1B1211CCD_correct_edge
J3, J11: Conn_01x04_Pin; PinHeader_1x04_P2.54mm_Vertical
J4, J5, J6, J7, J8, J9, J16, J17, J18, J19, J20, J21, J22, J23, J24, J25, J26, J27, J28, J29, J30, J31, J32, J33, J34, J35, J36, J37, J38, J39, J40, J41, J42, J43, J44, J45: Conn_01x08_Pin; PinHeader_1x08_P2.54mm_Vertical_smallcourtyard
J10: Conn_01x02_Pin; PinHeader_1x02_P2.54mm_Vertical
J12: Conn_01x02_Power; PinHeader_1x02_P2.54mm_Vertical
J13, J14, J15: AudioJack2_SwitchT; uxcell_audio_quarter_inch
J46: Conn_01x06_Pin; PinHeader_1x06_P2.54mm_Vertical
J47: Conn_01x07_Pin; PinSocket_1x07_P2.54mm_Vertical
J48: Conn_01x03_Pin; PinSocket_1x03_P2.54mm_Vertical
R1: 120; R_0805_2012_1.20x1.40mm_medpad
R2, R3, R4, R5, R6, R15, R16: 7500; R_0805_2012_1.20x1.40mm_medpad
R7, R8: 47; R_0805_2012_1.20x1.40mm_medpad
R9, R10, R11: 100K; R_0805_2012_1.20x1.40mm_medpad
R12, R13, R14: 0; R_0805_2012_1.20x1.40mm_medpad
R22, R26, R29: 10; R_0805_2012_1.20x1.40mm_medpad
R23, R25, R28: 4700; R_0805_2012_1.20x1.40mm_medpad
SW1, SW2: SW_DIP_x02; SW_DIP_SPSTx02_Slide_medpad
TP5: u1_com; TestPoint_Keystone_5000-5004_Miniature
TP6: canh; TestPoint_Keystone_5000-5004_Miniature
TP7: canl; TestPoint_Keystone_5000-5004_Miniature
TP8: d1; TestPoint_Keystone_5000-5004_Miniature
TP9: d2; TestPoint_Keystone_5000-5004_Miniature
TP10: d3; TestPoint_Keystone_5000-5004_Miniature
TP11: d4; TestPoint_Keystone_5000-5004_Miniature
TP12: s0; TestPoint_Keystone_5000-5004_Miniature
TP13: s1; TestPoint_Keystone_5000-5004_Miniature
TP14: s2; TestPoint_Keystone_5000-5004_Miniature
TP15: s3; TestPoint_Keystone_5000-5004_Miniature
TP19: u1_i0; TestPoint_Keystone_5000-5004_Miniature
TP21: gnd; TestPoint_Keystone_5000-5004_Miniature
TP22: V3.3; TestPoint_Keystone_5000-5004_Miniature
U1, U2, U3, U4, U5, U6: CD74HC4067; SOIC-24_7.5x15.4mm_P1.27mm_medpad
U7: Teensy4.1_all_pins; Teensy41_ringpads
U8: TCAN330G; SOIC-8_3.9x4.9mm_P1.27mm_medpad
U9: sca00_board
U11, U15, U16, U17, U18, U19: LDO; SOT-23-5_medpad
U12: Adafruit_28_CTouch_TFT; PinHeader_1x20_P2.54mm_Vertical
U13: midi_female; midi_rightangle_female

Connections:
+5V: C1.1, C5.1, C7.1, C9.1, C11.1, C13.1, F2.1, J12.2, U9.25 (v5), U11.1 (IN), U11.3 (EN), U15.1 (IN), U15.3 (EN), U16.1 (IN), U16.3 (EN), U17.1 (IN), U17.3 (EN), U18.1 (IN), U18.3 (EN), U19.1 (IN), U19.3 (EN)
/RD+: J2.4 (RD+), U7.26 (RX+)
/RD-: J2.6 (RD-), U7.25 (RX-)
/TD+: J2.1 (TD+), U7.30 (TX+)
/TD-: J2.3 (TD-), U7.29 (TX-)
GND: C1.2, C2.2, C3.2, C4.2, C5.2, C6.2, C7.2, C8.2, C9.2, C10.2, C11.2, C12.2, C13.2, C14.2, J1.2 (GND), J2.8 (GND), J2.9 (LEDG_K), J2.11 (LEDY_K), J3.1, J5.1, J5.2, J5.3, J5.4, J5.5, J5.6, J5.7, J5.8, J7.1, J7.2, J7.3, J7.4, J7.5, J7.6, J7.7, J7.8, J13.S, J14.S, J15.S, J16.1, J16.2, J16.3, J16.4, J16.5, J16.6, J16.7, J16.8, J17.1, J17.2, J17.3, J17.4, J17.5, J17.6, J17.7, J17.8, J22.1, J22.2, J22.3, J22.4, J22.5, J22.6, J22.7, J22.8, J23.1, J23.2, J23.3, J23.4, J23.5, J23.6, J23.7, J23.8, J28.1, J28.2, J28.3, J28.4, J28.5, J28.6, J28.7, J28.8, J29.1, J29.2, J29.3, J29.4, J29.5, J29.6, J29.7, J29.8, J34.1, J34.2, J34.3, J34.4, J34.5, J34.6, J34.7, J34.8, J35.1, J35.2, J35.3, J35.4, J35.5, J35.6, J35.7, J35.8, J40.1, J40.2, J40.3, J40.4, J40.5, J40.6, J40.7, J40.8, J41.1, J41.2, J41.3, J41.4, J41.5, J41.6, J41.7, J41.8, J47.7, R2.2, R3.2, R4.2, R5.2, R6.2, R15.2, R16.2, R22.2, R26.2, R29.2, SW1.3, SW1.4, SW2.3, SW2.4, TP21.1, U1.12 (GND), U1.15 (E), U2.12 (GND), U2.15 (E), U3.12 (GND), U3.15 (E), U4.12 (GND), U4.15 (E), U5.12 (GND), U5.15 (E), U6.12 (GND), U6.15 (E), U7.1 (GND), U7.28 (GND), U7.40 (GND), U7.53 (GND), U8.2 (GND), U9.10 (gnd), U9.26 (gnd), U11.2 (GND), U11.4 (NC), U12.1 (GND), U12.11 (GND), U15.2 (GND), U15.4 (NC), U16.2 (GND), U16.4 (NC), U17.2 (GND), U17.4 (NC), U18.2 (GND), U18.4 (NC), U19.2 (GND), U19.4 (NC)
unnamed: D1.2 (A), TP8.1, U7.6 (4_BCLK2_D3)
unnamed: D1.1 (K), R2.1
unnamed: D2.2 (A), TP9.1, U7.7 (5_IN2_D2)
unnamed: D2.1 (K), R3.1
unnamed: D3.2 (A), TP10.1, U7.10 (8_IN1_GPUEN)
unnamed: D3.1 (K), R4.1
unnamed: D4.2 (A), TP11.1, U7.18 (26_MOSI1_TFTRST)
unnamed: D4.1 (K), R5.1
unnamed: D5.2 (A), U7.24 (32_OUT1B)
unnamed: D5.1 (K), R6.1
unnamed: D6.2 (A), U7.48 (20_A6_TP0), U9.3 (x1)
unnamed: D6.1 (K), R15.1
unnamed: D7.2 (A), U7.49 (21_A7_TP1), U9.2 (x0)
unnamed: D7.1 (K), R16.1
unnamed: F1.1, J1.1 (VOUT)
unnamed: J2.10 (LEDG_A), U7.27 (LED)
unnamed: J2.12 (LEDY_A), U7.51 (23_A9_TP3)
unnamed: C3.1, J2.2 (TCT), J2.5 (RCT)
unnamed: C2.1, J4.1, J4.2, J4.3, J4.4, J4.5, J4.6, J4.7, J4.8, J6.1, J6.2, J6.3, J6.4, J6.5, J6.6, J6.7, J6.8, U1.24 (VCC), U11.5 (OUT)
unnamed: J8.1, TP19.1, U1.9 (I0)
unnamed: J8.2, U1.8 (I1)
unnamed: J8.3, U1.7 (I2)
unnamed: J8.4, U1.6 (I3)
unnamed: J8.5, U1.5 (I4)
unnamed: J8.6, U1.4 (I5)
unnamed: J8.7, U1.3 (I6)
unnamed: J8.8, U1.2 (I7)
unnamed: J9.1, U1.23 (I8)
unnamed: J9.2, U1.22 (I9)
unnamed: J9.3, U1.21 (I10)
unnamed: J9.4, U1.20 (I11)
unnamed: J9.5, U1.19 (I12)
unnamed: J9.6, U1.18 (I13)
unnamed: J9.7, U1.17 (I14)
unnamed: J9.8, U1.16 (I15)
unnamed: J10.1, R1.2, TP7.1, U8.6 (CANL)
unnamed: J10.2, R1.1, TP6.1, U8.7 (CANH)
unnamed: F1.2, J12.1
unnamed: C6.1, J18.1, J18.2, J18.3, J18.4, J18.5, J18.6, J18.7, J18.8, J19.1, J19.2, J19.3, J19.4, J19.5, J19.6, J19.7, J19.8, U2.24 (VCC), U9.24 (v33a), U15.5 (OUT)
unnamed: J20.1, U2.9 (I0)
unnamed: J20.2, U2.8 (I1)
unnamed: J20.3, U2.7 (I2)
unnamed: J20.4, U2.6 (I3)
unnamed: J20.5, U2.5 (I4)
unnamed: J20.6, U2.4 (I5)
unnamed: J20.7, U2.3 (I6)
unnamed: J20.8, U2.2 (I7)
unnamed: J21.1, U2.23 (I8)
unnamed: J21.2, U2.22 (I9)
unnamed: J21.3, U2.21 (I10)
unnamed: J21.4, U2.20 (I11)
unnamed: J21.5, U2.19 (I12)
unnamed: J21.6, U2.18 (I13)
unnamed: J21.7, U2.17 (I14)
unnamed: J21.8, U2.16 (I15)
unnamed: C8.1, J24.1, J24.2, J24.3, J24.4, J24.5, J24.6, J24.7, J24.8, J25.1, J25.2, J25.3, J25.4, J25.5, J25.6, J25.7, J25.8, U3.24 (VCC), U16.5 (OUT)
unnamed: J26.1, U3.9 (I0)
unnamed: J26.2, U3.8 (I1)
unnamed: J26.3, U3.7 (I2)
unnamed: J26.4, U3.6 (I3)
unnamed: J26.5, U3.5 (I4)
unnamed: J26.6, U3.4 (I5)
unnamed: J26.7, U3.3 (I6)
unnamed: J26.8, U3.2 (I7)
unnamed: J27.1, U3.23 (I8)
unnamed: J27.2, U3.22 (I9)
unnamed: J27.3, U3.21 (I10)
unnamed: J27.4, U3.20 (I11)
unnamed: J27.5, U3.19 (I12)
unnamed: J27.6, U3.18 (I13)
unnamed: J27.7, U3.17 (I14)
unnamed: J27.8, U3.16 (I15)
unnamed: C10.1, J30.1, J30.2, J30.3, J30.4, J30.5, J30.6, J30.7, J30.8, J31.1, J31.2, J31.3, J31.4, J31.5, J31.6, J31.7, J31.8, U4.24 (VCC), U17.5 (OUT)
unnamed: J32.1, U4.9 (I0)
unnamed: J32.2, U4.8 (I1)
unnamed: J32.3, U4.7 (I2)
unnamed: J32.4, U4.6 (I3)
unnamed: J32.5, U4.5 (I4)
unnamed: J32.6, U4.4 (I5)
unnamed: J32.7, U4.3 (I6)
unnamed: J32.8, U4.2 (I7)
unnamed: J33.1, U4.23 (I8)
unnamed: J33.2, U4.22 (I9)
unnamed: J33.3, U4.21 (I10)
unnamed: J33.4, U4.20 (I11)
unnamed: J33.5, U4.19 (I12)
unnamed: J33.6, U4.18 (I13)
unnamed: J33.7, U4.17 (I14)
unnamed: J33.8, U4.16 (I15)
unnamed: C12.1, J36.1, J36.2, J36.3, J36.4, J36.5, J36.6, J36.7, J36.8, J37.1, J37.2, J37.3, J37.4, J37.5, J37.6, J37.7, J37.8, U5.24 (VCC), U18.5 (OUT)
unnamed: J38.1, U5.9 (I0)
unnamed: J38.2, U5.8 (I1)
unnamed: J38.3, U5.7 (I2)
unnamed: J38.4, U5.6 (I3)
unnamed: J38.5, U5.5 (I4)
unnamed: J38.6, U5.4 (I5)
unnamed: J38.7, U5.3 (I6)
unnamed: J38.8, U5.2 (I7)
unnamed: J39.1, U5.23 (I8)
unnamed: J39.2, U5.22 (I9)
unnamed: J39.3, U5.21 (I10)
unnamed: J39.4, U5.20 (I11)
unnamed: J39.5, U5.19 (I12)
unnamed: J39.6, U5.18 (I13)
unnamed: J39.7, U5.17 (I14)
unnamed: J39.8, U5.16 (I15)
unnamed: C14.1, J42.1, J42.2, J42.3, J42.4, J42.5, J42.6, J42.7, J42.8, J43.1, J43.2, J43.3, J43.4, J43.5, J43.6, J43.7, J43.8, J47.3, R23.2, R25.2, R28.2, U6.24 (VCC), U19.5 (OUT)
unnamed: J44.1, U6.9 (I0)
unnamed: J44.2, U6.8 (I1)
unnamed: J44.3, U6.7 (I2)
unnamed: J44.4, U6.6 (I3)
unnamed: J44.5, U6.5 (I4)
unnamed: J44.6, U6.4 (I5)
unnamed: J44.7, U6.3 (I6)
unnamed: J44.8, U6.2 (I7)
unnamed: J45.1, U6.23 (I8)
unnamed: J45.2, U6.22 (I9)
unnamed: J45.3, U6.21 (I10)
unnamed: J45.4, U6.20 (I11)
unnamed: J45.5, U6.19 (I12)
unnamed: J45.6, U6.18 (I13)
unnamed: J45.7, U6.17 (I14)
unnamed: J45.8, U6.16 (I15)
unnamed: J13.T, J46.1, R23.1
unnamed: J13.TN, J46.2, R22.1
unnamed: J14.T, J46.3, R25.1
unnamed: J14.TN, J46.4, R26.1
unnamed: J15.T, J46.5, R28.1
unnamed: J15.TN, J46.6, R29.1
unnamed: J47.1, U7.31 (33_MCLK2_L0), U12.19 (CARD_CS)
unnamed: J47.2, R11.2, U7.32 (34_RC8_L1), U12.20 (CARD_Detect)
unnamed: J47.4, R12.2, U12.5 (MISO)
unnamed: J47.5, R13.2, U12.4 (CLK)
unnamed: J47.6, R14.2, U12.6 (MOSI)
unnamed: C4.1, J48.1, R8.1, R9.1, R10.1, R11.1, TP22.1, U7.52 (3.3VOUT), U8.3 (VCC), U9.1 (v33d), U12.2 (Vin_3.3V)
unnamed: TP5.1, U1.1 (COM), U9.22 (ain0)
unnamed: TP12.1, U1.10 (S0), U2.10 (S0), U3.10 (S0), U4.10 (S0), U5.10 (S0), U6.10 (S0), U7.36 (38_A14_L5)
unnamed: TP13.1, U1.11 (S1), U2.11 (S1), U3.11 (S1), U4.11 (S1), U5.11 (S1), U6.11 (S1), U7.35 (37_CS_L4)
unnamed: TP14.1, U1.14 (S2), U2.14 (S2), U3.14 (S2), U4.14 (S2), U5.14 (S2), U6.14 (S2), U7.34 (36_CS_L3)
unnamed: TP15.1, U1.13 (S3), U2.13 (S3), U3.13 (S3), U4.13 (S3), U5.13 (S3), U6.13 (S3), U7.33 (35_TX8_L2)
unnamed: U2.1 (COM), U9.21 (ain1)
unnamed: U3.1 (COM), U9.20 (ain2)
unnamed: U4.1 (COM), U9.19 (ain3)
unnamed: U5.1 (COM), U9.18 (ain4)
unnamed: U6.1 (COM), U9.17 (ain5)
unnamed: SW2.1, U7.2 (0_CS1_D7)
unnamed: R7.1, U7.3 (1_MISO1_D6)
unnamed: SW2.2, U7.4 (2_OUT2_D5)
unnamed: SW1.1, U7.5 (3_LRCLK2_D4)
unnamed: F2.2, U7.54 (5VI/O)
unnamed: R14.1, U7.13 (11_MOSI), U9.13 (din)
unnamed: R12.1, U7.14 (12_MISO), U9.11 (dout)
unnamed: R13.1, U7.41 (13_SCK), U9.12 (sclk)
unnamed: U7.42 (14_A0), U9.9 (x7)
unnamed: U7.43 (15_A1), U9.8 (x6)
unnamed: U7.44 (16_A2), U9.7 (x5)
unnamed: U7.45 (17_A3), U9.6 (x4)
unnamed: U7.46 (18_SDA_A4), U9.5 (x3)
unnamed: U7.47 (19_SCL_A5), U9.4 (x2)
unnamed: SW1.2, U7.50 (22_A8_TP2)
unnamed: U7.20 (28_RX7), U8.8 (S)
unnamed: U7.21 (29_TX7), U8.5 (SHDN)
unnamed: U7.22 (30_CRX3), U8.4 (RXD)
unnamed: U7.23 (31_CTX3), U8.1 (TXD)
unnamed: U7.37 (39_A15_L6), U9.14 (x8)
unnamed: U7.38 (40_A16_L7), U9.15 (x9)
unnamed: U7.39 (41_A17), U9.16 (x10)
unnamed: U12.3 (3Vo), U12.15 (IM3), U12.16 (IM2), U12.17 (IM1)
unnamed: U7.19 (27_SCK1_A13_TFCARDCS), U12.7 (CS)
unnamed: U7.12 (10_CS), U12.8 (D/C)
unnamed: U7.8 (6_OUT1D_D1), U12.12 (IRQ)
unnamed: U7.9 (7_OUT1A_D0), U12.10 (LITE)
unnamed: U7.11 (9_OUT1C_GPUOK), U12.9 (RESET)
unnamed: R9.2, U7.16 (24_SCL2_A10), U12.14 (SCL)
unnamed: R10.2, U7.17 (25_SDA2_A11), U12.13 (SDA)
unnamed: R7.2, U13.5 (DATA)
unnamed: R8.2, U13.4 (VREF)


Board: 2 copper layers, 215.9 x 101.6 mm, 131 parts (0 on the bottom side), 183 nets.

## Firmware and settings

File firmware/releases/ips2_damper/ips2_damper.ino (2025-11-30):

// Copyright (C) 2025 Greg C. Zweigle
//
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
// Location of documentation, code, and design:
// https://github.com/gzweigle/open-hybrid-piano
// https://github.com/stem-piano
//
// src_damper.cpp
//
// For ips pcb version 2.X
// For sca pcb version 0.0
//
// Main code for damper board of stem piano.
//
// stem piano is an open source hybrid digital piano.
//

#include "stem_piano_ips2.h"

#include "damper_settings.h"
#include "six_channel_analog_00.h"
#include "board2board.h"
#include "calibration_position.h"
#include "damper_status.h"
#include "network.h"
#include "nonvolatile.h"
#include "switches.h"
#include "testpoint_led.h"
#include "timing.h"
#include "tft_display.h"

DamperSettings Set;
SixChannelAnalog00 Adc;
Board2Board B2B;
CalibrationPosition CalP;
DamperStatus DStat;
Network Eth;
Nonvolatile Nonv;
Switches SwIPS1;
Switches SwIPS2;
Switches SwSCA1;
Switches SwSCA2;
TestpointLed Tpl;
Timing Tmg;
TftDisplay Tft;

void setup(void) {

  // Serial port setup.
  Serial.begin(9600);
  Serial.println(".");
  Serial.println(".");
  Serial.println("welcome to stem piano by gcz");
  Serial.println("an open source, hybrid piano");
  Serial.println(".");
  Serial.println(".");

  // Important information.
  Serial.println("Hardware required:");
  Serial.println("  IPS2.X hammer board.");
  Serial.println("  SCA0.0 analog board.");
  Serial.println("  HPS 0.8, 0.7, or 0.4 sensor board (any board meeting spec is also ok).");
  Serial.println("License: GNU GPLv3 - for documentation, code, and design see:");
  Serial.println("https://github.com/gzweigle/open-hybrid-piano");
  Serial.println("https://github.com/stem-piano");
  Serial.println(".");
  Serial.println(".");

  // Load the settings. Must be first in the setup() function.
  Set.SetAllSettingValues();

  // Notification messages.
  if (Set.debug_level >= DEBUG_INFO) {
    Serial.println("Beginning damper board initialization.");
  }
  Tft.Setup(Set.using_display, Set.debug_level);
  Tft.HelloWorld();

  // Initialize the nonvolatile memory.
  // Initialize early in case any setup() uses storage.
  Nonv.Setup(Set.debug_level);

  // Setup reading the switches.
  SwIPS1.Setup(Set.switch_debounce_micro,
  Set.switch11_ips_pin, Set.switch12_ips_pin, Set.debug_level);
  SwIPS2.Setup(Set.switch_debounce_micro,
  Set.switch21_ips_pin, Set.switch22_ips_pin, Set.debug_level);
  SwSCA1.Setup(Set.switch_debounce_micro,
  Set.switch11_sca_pin, Set.switch12_sca_pin, Set.debug_level);
  SwSCA2.Setup(Set.switch_debounce_micro,
  Set.switch21_sca_pin, Set.switch22_sca_pin, Set.debug_level);

  // Setup the analog front-end and the board-to-board communication.
  // Physically connecting the board-to-board link is optional and
  // only required if using a separate set of sensors for the dampers.
  // These two classes are common to hammer and pedal boards.
  Adc.Setup(Set.adc_spi_clock_frequency, Set.adc_is_differential,
  Set.using18bitadc, Set.sensor_v_max, Set.adc_reference,
  Set.adc_global_scale, Set.reorder_list, &Tpl);
  B2B.Setup(Set.canbus_enable);

  // Diagnostics and status
  DStat.Setup(&Tpl, Set.debug_level);

  // Common on hammer and pedal board: Ethernet, test points, TFT display, etc.
  CalP.Setup(Set.calibration_threshold, Set.debug_level, &Nonv);
  Eth.Setup(Set.true_for_tcp_else_udp, Set.computer_ip, Set.teensy_ip,
    Set.network_port, SwIPS2.direct_read_switch_2(), Set.debug_level);
  Tpl.Setup();
  Tmg.Setup(Set.adc_sample_period_microseconds, Set.debug_level);

  if (Set.test_index >= 0) {
    Serial.println("WARNING - In high-speed test mode.");
    Serial.println("MIDI is disabled.");
  }

  // Ready to be a piano (damper).
  if (Set.debug_level >= DEBUG_INFO) {
    Serial.println("Finished damper board initialization.");
  }
  delay(1000);
  Tft.Clear();

}

// After startup, wait before sending anything to MIDI
// in order to avoid any potential startup transients.
int startup_counter = 0;

// Switches.
bool switch_enable_ethernet;
bool switch_require_tcp_connection;
bool switch_tft_display;
bool switch_freeze_cal_values;
bool switch_disable_and_reset_calibration;

// Data from ADC.
unsigned int raw_samples[NUM_CHANNELS];
unsigned int raw_samples_reversed[NUM_CHANNELS];
unsigned int raw_samples_reordered[NUM_CHANNELS];
int position_adc_counts[NUM_CHANNELS];

// Damper, hammer, and pedal data.
float damper_position[NUM_CHANNELS], calibrated_floats[NUM_CHANNELS],
position_floats[NUM_CHANNELS];

// Damper threshold for display
float damper_threshold_low = 0.33;
float damper_threshold_med = 0.50;
float damper_threshold_high = 0.75;

void loop() {

  Tmg.WarnOnProcessingInterval();
  DStat.DisplayProcessingIntervalStart();

  // Measure every processing interval so the pickup and
  // dropout timers update. Later, when a switch is read,
  // what is actually read is the internal state of timers.
  SwIPS1.updatePuDoState("IPS11", "IPS12");
  SwIPS2.updatePuDoState("IPS21", "IPS22");
  SwSCA2.updatePuDoState("SCA21", "SCA22");
  SwSCA1.updatePuDoState("SCA11", "SCA12");

  // Read all switch inputs.

  // ips_sw1_position2 (ENABLE_TFT).
  switch_tft_display = SwIPS1.read_switch_2();

  // ips_sw2_position2 (ENABLE_ETHERNET).
  switch_enable_ethernet = SwIPS2.read_switch_2();

  // ips_sw2_position1 (REQUIRE_TCP).
  switch_require_tcp_connection = SwIPS2.read_switch_1();

  // sca_sw1_position2 (FREEZE_CAL_VALUES).
  switch_freeze_cal_values = SwSCA1.read_switch_2();

  // sca_sw1_positon1 (DELETE_CAL_VALUES).
  switch_disable_and_reset_calibration = SwSCA1.read_switch_1();

  // When the TFT is operational.
  // Slow down sampling because the TFT takes a long time for
  // processing. But, do keep the sampling going so that the TFT
  // can display things like maximum and minimum hammer positions.
  if (switch_tft_display == true) {
    switch_freeze_cal_values = true; // Ignore switch value.
    Tmg.ResetInterval(Set.adc_sample_period_microseconds_during_tft);
  }
  else {
    Tmg.ResetInterval(Set.adc_sample_period_microseconds);
  }

  // This if statement determines the sample rate.
  // Everything below in this file runs at the sample rate.
  if (Tmg.AllowProcessing() == true) {

    Tpl.SetTp8(true); // Front left test point asserts during processing.

    // Get damper data from ADC.
    Adc.GetNewAdcValues(raw_samples, Set.test_index);

    // Reverse the back row since a damper board is
    // rotated 180 degrees compared to a hammer board.
    // Use NUM_CHANNELS - 8 because not reversing the
    // eight inputs typically used for pedals.
    for (int ind = 0; ind < NUM_CHANNELS - 8; ind++) {
      raw_samples_reversed[ind] = raw_samples[NUM_CHANNELS - ind - 1 - 8];
    }

    // Reorder the back row.
    Adc.ReorderAdcValues(raw_samples_reordered, raw_samples_reversed);

    // Normalize the ADC values.
    Adc.NormalizeAdcValues(position_adc_counts, position_floats, raw_samples_reordered);

    // Undo the position errors due to physical tolerances.
    bool all_notes_using_cal = CalP.Calibration(switch_freeze_cal_values,
    switch_disable_and_reset_calibration, calibrated_floats, position_floats);

    // Zero out the signal from any unconnected pins to avoid noise
    // or anything else causing an unwanted piano note to play.
    for (int k = 0; k < NUM_CHANNELS; k++) {
      if (Set.connected_channel[k] == false) {
        position_adc_counts[k] = 0;
        calibrated_floats[k] = 0.0;
      }
    }

    B2B.SendDamperData(calibrated_floats);
    Eth.SendPianoPacket(calibrated_floats, calibrated_floats,
      switch_enable_ethernet, switch_require_tcp_connection, Set.test_index);

    if (Set.test_index < 0) {
      // Run the TFT display.
      Tft.Display(switch_tft_display, calibrated_floats, damper_position);
    }

    // Debug and display information.
    DStat.FrontLed(calibrated_floats, damper_threshold_low, damper_threshold_med,
    damper_threshold_high, Set.test_index);

    if (Set.test_index < 0) {
      DStat.LowerRightLed(all_notes_using_cal, Nonv.NonvolatileWasWritten());
      DStat.SCALed();
      DStat.EthernetLed();
      DStat.SerialMonitor(position_adc_counts, calibrated_floats,
      calibrated_floats[0], position_floats[0],
      calibrated_floats[1], position_floats[1],
      calibrated_floats[2], position_floats[2],
      calibrated_floats[3], position_floats[3],
      calibrated_floats[4], position_floats[4],
      calibrated_floats[5], position_floats[5],
      calibrated_floats[6], position_floats[6],
      calibrated_floats[7], position_floats[7]);
    }

    Tpl.SetTp8(false);

  }

  DStat.DisplayProcessingIntervalEnd();
}

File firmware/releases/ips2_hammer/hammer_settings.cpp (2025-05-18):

// Copyright (C) 2025 Greg C. Zweigle
//
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
// Location of documentation, code, and design:
// https://github.com/gzweigle/open-hybrid-piano
// https://github.com/stem-piano
//
// hammer_settings.cpp
//
// For ips pcb version 2.X
// For sca pcb version 0.0
//
// Common location for all settings related to the system.
//
// WARNING - Board consistency.
// The following values must be identical on hammer and damper boards:
//    - adc_sample_period_microseconds.

#include "hammer_settings.h"

HammerSettings::HammerSettings() {}

void HammerSettings::SetAllSettingValues() {

  // Debug. See stem_piano_ips2.h for information.
  // DEBUG_NONE = Nothing displayed except startup info.
  // DEBUG_INFO = Occasional code state information.
  // DEBUG_NOTES = Above plus info about note changes.
  // DEBUG_STATS = Above plus occasional statistics.
  // DEBUG_ALG = Above plus algorithm details.
  // DEBUG_ALL = Above plus useless stuff.
  debug_level = DEBUG_NOTES;
  Serial.print("Debug level is set to ");
  Serial.println(debug_level);

  // Avoid risk of anything bad happening on startup. Probably not needed.
  // Wait this number of ADC samples before allow piano sounds.
  startup_counter_value = 100;

  ////////
  // ADC settings.

  // Max is 70e6 per the ADC datasheet.
  // Set at the lowest value needed to get all data clocked
  // out in time to meet the adc_sample_period_microseconds value.
  adc_spi_clock_frequency = 60000000;

  // High sample rate data acquisition mode.
  // If >= 0, all piano functions are disabled except test_index channel. 
  // Because all functions are disabled, it is possible to set the sample
  // rate approximately 10x faster than during normal operation.
  test_index = -1;
  
  // Must be longer than the time to sample and collect all NUM_CHANNELS
  // data from the ADC plus the time for processing all of the data.
  // WARNING - For normal operation, this value must match damper board value.
  adc_sample_period_microseconds = 250;
  
  if (debug_level >= DEBUG_INFO) {
    Serial.print("The sample period is set to ");
    Serial.print(adc_sample_period_microseconds);
    Serial.println(" microseconds.");
    Serial.println("The sample period value must match on hammer and damper boards.");
  }

  // When the TFT is running, slow everything down because the TFT
  // processing takes a long time.
  adc_sample_period_microseconds_during_tft = 100000;

  // The analog circuitry in front of ADC is not differential.
  // Therefore, if using a differential ADC, lose a bit.
  adc_is_differential = true;

  // Presently support a 16-bit or 18-bit ADC.
  using18bitadc = false;

  // Historically, ADC changes during development resulted in
  // 1.2V, 2.5V, 3.0V, and 3.3V for adc_reference. 
  // Also, ADC changes during development resulted in using
  // 1.2V and 3.3V for sensor_v_max. Therefore, the sensor_v_max
  // and adc_reference setttings are useful during development to
  // support connecting older and newer ADC systems together.

  // The maximum voltage output by the sensor when hammer is at highest position.
  sensor_v_max = 2.5;

  // Reference value on ADC. When the output of the sensor is at this voltage,
  // the ADC outputs its maximum value.
  adc_reference = 2.5;

  // A global scaling applied to all ADC inputs.
  // Normally set to 1.0.
  adc_global_scale = 0.5;

  ////////
  // Gain control.
  // The combination of piano action plus mechanical structure
  // built for a stem piano could result in a different velocity
  // minimum and maximum values per piano. Use this scaling factor
  // when converting velocity in meters per second to MIDI values.
  velocity_scale = 0.35;

  // Any MIDI velocity equal to this value or larger is muted.
  // Typically set to 127. But is user configurable. Assumption
  // is that normal piano playing won't use a volume of 127 but a
  // problem could. For example, a firmware or mechanical issue.
  // To disable, set >= max MIDI velocity (128 most likely).
  maximum_midi_velocity = 127;

  ////////
  // Switch settings.
  switch_debounce_micro = 500000; // Read DIP switches at this interval, microseconds.
  switch11_ips_pin = 3;
  switch12_ips_pin = 22;
  switch21_ips_pin = 0;
  switch22_ips_pin = 2;
  switch11_sca_pin = 19;
  switch12_sca_pin = 18;
  switch21_sca_pin = 17;
  switch22_sca_pin = 16;

  ////////
  // Calibration Settings.
  calibration_threshold = 0.5;

  ////////
  // Damper Settings.

  // When the damper position crosses this percentage of max-min
  // damper position, declare a damper event.
  damper_threshold = 0.5;

  // Magic value to get velocity in range [-1,0].
  damper_velocity_scaling = 0.025;

  ////////
  // Hammer Settings.
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

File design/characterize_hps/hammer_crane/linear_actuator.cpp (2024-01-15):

// Copyright (C) 2024 Greg C. Zweigle
//
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
// Location of documentation, code, and design:
// https://github.com/gzweigle/DIY-Grand-Digital-Piano
//
// linear_actuator.cpp
//
// Control linear actuator through L298N board.

#include "linear_actuator.h"

LinearActuator::LinearActuator() {}

void LinearActuator::Setup(bool arduino_workaround) {
  arduino_workaround_ = arduino_workaround;

  if (arduino_workaround_ == true) {
    // For some Arduino Nano the following does not work:
    //   DigitalWrite(PBX, <value>);
    //   X = 0, 1, 2, ...
    // Therefore, write registers directly.
    DDRB |= _BV(0);   // Set PB0 as output.
    DDRB |= _BV(1);   // Set PB1 as output.
  }
  else {
    pinMode(PB0, OUTPUT);
    pinMode(PB1, OUTPUT);
  }
}

// Position input from linear actuator to 10-bit internal ADC.
// Tests show resistance for the linear actuator ranges from:
//   45 = fully retracted.
//   473 = fully extended.
float LinearActuator::GetPositionRatio() {
  float resistance, ratio;
  resistance = static_cast<float>(analogRead(A7));
  ratio = resistance - 45.0;
  ratio /= (473.0 - 45.0);
  if (ratio < 0) {
    ratio = 0;
  }
  else if (ratio > 1.0) {
    ratio = 1.0;
  }
  return ratio;
}

void LinearActuator::Extend() {
  if (arduino_workaround_ == true) {
    PORTB |= _BV(0);
    PORTB &= ~(_BV(1));
  }
  else {
    digitalWrite(PB0, HIGH);
    digitalWrite(PB1, LOW);
  }
}

void LinearActuator::Retract() {
  if (arduino_workaround_ == true) {
    PORTB &= ~(_BV(0));
    PORTB |= _BV(1);
  }
  else {
    digitalWrite(PB0, LOW);
    digitalWrite(PB1, HIGH);
  }
}

void LinearActuator::Stop() {
  if (arduino_workaround_ == true) {
    PORTB &= ~(_BV(0));
    PORTB &= ~(_BV(1));
  }
  else {
    digitalWrite(PB0, LOW);
    digitalWrite(PB1, LOW);
  }
}

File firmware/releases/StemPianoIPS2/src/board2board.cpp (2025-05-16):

// Copyright (C) 2025 Greg C. Zweigle
//
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
// Location of documentation, code, and design:
// https://github.com/gzweigle/open-hybrid-piano
// https://github.com/stem-piano
//
// board2board.cpp
//
// This code runs on ips pcb version 2.X
//
// Transfer damper position from damper board to hammer board using CAN Bus.
//
// The code packs and unpacks position data from damper of 88 piano keys into
// the 64*8 = 512 bits of CAN FD as follows:
// A0  - 4 bits
// A#0 - 4 bits
// B0  - 4 bits
// C1  - 4 bits
// C#1 - 6 bits
//  :    :
// G#7 - 6 bits
// A7  - 4 bits
// A#7 - 4 bits
// B7  - 4 bits
// C8  - 4 bits
// From the above: (4+4)*4 + 80*6 = 512.  So, it fits.
//
// The boards have enough pins to extend a keyboard beyond 88 keys.
// In this case, the mapping described above would need to change
// in order to fit the extra keys into the 512 available bits.
//
// TODO - Only supports 88 dampers. If a piano with more keys
//        is built, and if want dampers on those keys, then will
//        need to extend to the extra keys.

#include "board2board.h"

Board2Board::Board2Board() {}

void Board2Board::Setup(bool enable) {

  enable_ = enable;

  // Connected to CAN Bus driver IC but not using these features
  // of the IC. Drive low and never change the state.
  pinMode(28, OUTPUT);
  pinMode(29, OUTPUT);
  digitalWrite(28, LOW);
  digitalWrite(29, LOW);

  if (enable_ == true) {
    CANFD_timings_t config;
    config.baudrate = 1000000;
    config.baudrateFD = 2000000;
    config.bus_length = 1;
    config.clock = CLK_24MHz;
    config.propdelay = 190;
    config.sample = 70;
    can_.begin();
    can_.setRegions(64);
    can_.setBaudRate(config);

    msg_tx_.id = 0x100;
    msg_tx_.len = CANBUS_LENGTH;
    for (int ind = 0; ind < msg_tx_.len; ind++) {
      msg_tx_.buf[ind] = 0;
    }
  }
}

// Pack the damper data into CAN Bus array and send it.
// This function is called by the damper board code.
void Board2Board::SendDamperData(const float *position) {
  if (enable_ == true) {
    int p_int[NUM_CHANNELS];
    int p_int_limit;
    for (int ind = 0; ind < NUM_CHANNELS; ind++) {
      if (ind < 4 || ind > 83) {
        p_int_limit = static_cast<int>(16.0 * position[ind]);
        if (p_int_limit > 15)
          p_int_limit = 15;
        else if (p_int_limit < 0)
          p_int_limit = 0;
        p_int[ind] = p_int_limit;
      }
      else {
        p_int_limit = static_cast<int>(64.0 * position[ind]);
        if (p_int_limit > 63)
          p_int_limit = 63;
        else if (p_int_limit < 0)
          p_int_limit = 0;
        p_int[ind] = p_int_limit;
      }
    }
    // First 4 and last 4 of 88 keys are 4 bits each.
    msg_tx_.buf[0]  = (p_int[0]<<4)  | p_int[1];
    msg_tx_.buf[1]  = (p_int[2]<<4)  | p_int[3];
    msg_tx_.buf[62] = (p_int[84]<<4) | p_int[85];
    msg_tx_.buf[63] = (p_int[86]<<4) | p_int[87];
    // The middle 80 keys are 6 bits, which is 480 total bits.
    // The following pattern repeats 480/8/3 = 20 times.
    // AAAAAABB, BBBBCCCC, CCDDDDDD
    for (int ind = 0; ind < 20; ind++) {
      msg_tx_.buf[3*ind+2] = ( p_int[4*ind+4]<<2)       | ((p_int[4*ind+5]>>4)&0x03);
      msg_tx_.buf[3*ind+3] = ((p_int[4*ind+5]<<4)&0xF0) | ((p_int[4*ind+6]>>2)&0x0F);
      msg_tx_.buf[3*ind+4] = ((p_int[4*ind+6]<<6)&0xC0) | ( p_int[4*ind+7]    &0x3F);
    }
    can_.write(msg_tx_);
  }
}
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

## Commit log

2022-01-10 hammer samples and quick analysis
2022-01-10 clarify velocity, add figures
2022-01-10 zoom in for velocity figure
2022-02-08 simple get ADC example
2023-03-13 new single board option
2023-06-09 dpp board bringup code
2023-06-09 damper board
2023-07-29 bill of materials
2023-07-29 update bill of materials
2023-08-09 hammer position sensor 0.6 pcb
    [hps06-B_Cu.gbr, hps06-B_Mask.gbr, hps06-B_Paste.gbr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]
2023-08-09 hammer position sensor pcb 0.6
2023-08-09 hammer position sensor pcb 0.4
    [hps04-B_Cu.gbr, hps04-B_Mask.gbr, hps04-B_Paste.gbr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]
2023-08-17 power supplies
2023-08-17 power supply
2023-08-17 fuse wording
2023-11-26 sca00 PCB plus FW releases
    [sca00-B_Cu.gbr, sca00-B_Mask.gbr, sca00-B_Paste.gbr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]
2023-11-26 sca00 PCB
2023-11-26 sca00 PCB (2)
2023-11-26 sca00 schematic
2023-11-26 ADC driver
2023-11-26 SCA 2.0 PCB
    [ips20-B_Cu.gbr, ips20-B_Mask.gbr, ips20-B_Paste.gbr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]
2023-11-26 IPS 2.0 PCB
2023-12-10 doc- clarify SCA board count
2024-01-07 hps07 g
    [hps07-B_Cu.gbr, hps07-B_Mask.gbr, hps07-B_Paste.gbr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]
2024-04-07 spec hammer and sensor bars
2024-04-07 add KiCad projects
    [hps04.kicad_pcb, hps04.kicad_sch, hps06.kicad_pcb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]
2024-04-08 kicad info link
2024-04-20 calibration - partial
2024-04-21 refactor status and led
2024-04-22 note parts back of PCB
2024-05-04 new config switch func
2024-05-04 velocity calibration
2024-05-05 fix extra serial info
    [auto_mute.cpp, calibration_sensor.cpp]
2024-05-05 15-14ms and hps08 gerber
    [hps08-B_Cu.gbr, hps08-B_Mask.gbr, hps08-B_Paste.gbr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]
2024-05-12 better fuse approach
2024-06-08 add PLS circuit board
    [pls00-B_Cu.gbr, pls00-B_Mask.gbr, pls00-B_Paste.gbr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]
2024-06-09 fix issue 51 - setup network
    [network.cpp, src_hammer.cpp, switches.cpp]
2024-06-09 issue 29 - midi buffer
    [src_hammer.cpp]
2024-06-09 hps08 and pls00 kicad
    [hps08.kicad_pcb, hps08.kicad_sch, pls00.kicad_pcb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]
2024-06-10 issue 48 - indicate eeprom write
    [hammer_status.cpp, nonvolatile.cpp, src_hammer.cpp]
2024-06-15 issue 45 - LDO current
2024-06-16 resistor values and hps info
2024-06-20 issue 53 - interposer board
    [aceA00-B_Cu.gbr, aceA00-B_Mask.gbr, aceA00-B_Paste.gbr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]
2024-06-23 issue 62 - pedal resistors
2024-06-29 issues 61(speedup) and 59(high speed test mode)
    [hammer_settings.cpp, hammer_status.cpp, network.cpp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]
2024-06-29 issue 60 - clipping
    [calibration_sensor.cpp]
2024-06-29 issue 42 - max midi
    [auto_mute.cpp, hammer_settings.cpp, midiout.cpp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]
2024-06-30 issue 46 - velocity scaling
    [calibration_position.cpp, calibration_velocity.cpp, hammer_settings.cpp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]
2024-07-01 issue 65 - adj damper thresh
    [dsp_damper.cpp, hammer_settings.cpp, hammer_status.cpp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]
2024-07-01 issue 68 - ACE KiCad
    [aceA00.kicad_pcb, aceA00.kicad_sch]
2024-07-05 issue 69 (KiCad 8), 70 (label wrong side)
    [aceA00.kicad_pcb, aceA00.kicad_sch, aceA01.kicad_pcb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]
2024-07-14 clarify fuse
2024-07-15 issue 78 - cut 5V pad
2024-07-21 issue 80 - cal double prec
    [calibration_position.cpp, hammer_settings.cpp, src_hammer.cpp]
2024-07-21 issue 31 - update damper code
    [damper_settings.cpp, damper_status.cpp, src_damper.cpp]
2024-07-26 ips power doc update
2024-07-26 ips power doc
2024-07-27 surface mount replace video link
2024-07-27 sensor info
2024-08-10 issue 55 - velocity algorithm
    [hammer_settings.cpp, src_hammer.cpp]
2024-08-10 issue 84 - init nonv memory
    [nonvolatile.cpp]
2024-08-10 issue 81 - store cal as doubles
    [calibration_position.cpp, calibration_velocity.cpp, nonvolatile.cpp]
2024-09-02 issues 85 (adc scaling) and 86 (filter length)
    [hammer_settings.cpp, six_channel_analog_00.cpp, src_hammer.cpp]
2024-09-05 issue 88 - power jumper
2024-09-09 issue 92 - tft compile error
    [tft_display.cpp]
2024-09-28 issue 97, 91, add new videos
    [network.cpp, src_hammer.ino]
2024-09-28 Issue 103 - fix comment
    [hammer_settings.cpp]
2024-09-29 issue - 100 - custom wiring in FW
    [hammer_settings.cpp, six_channel_analog_00.cpp, src_damper.ino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]
2024-10-02 experimental ACE with ethernet, aka 8P8C connectors
    [aceA01-eth.kicad_pcb, aceA01-eth.kicad_sch]
2024-10-02 footprint and symbol for the stacked 8P8C
2025-01-07 issue 101 - damper board compile
    [damper_settings.cpp, src_damper.ino]
2025-04-23 issue 113 - add tcp streaming
    [hammer_settings.cpp, network.cpp, src_hammer.ino]
2025-04-26 issue 114 - tcp long delay
    [network.cpp]
2025-04-26 issue 115 - improve debug messages
    [hammer_settings.cpp]
2025-04-26 issue 118 - add display processor burden
    [hammer_status.cpp]
2025-04-26 issue 115 (debug) and 117 (link)
    [auto_mute.cpp, board2board.cpp, calibration_position.cpp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]
2025-04-26 issue 101 - damper board compiling
    [damper_settings.cpp, damper_status.cpp, src_damper.ino]
2025-05-05 issue 116 - fix processor burden overrun on print
    [hammer_status.cpp]
2025-05-05 issue 120 - speed up sample rate
    [hammer_settings.cpp]
2025-05-10 fix minor damper status interval bug
    [damper_settings.cpp, damper_status.cpp]
2025-05-12 issue 121 - damper board bug
    [midiout.cpp]
2025-05-16 issue 122 - short sustain bug
    [board2board.cpp]
2025-05-18 issue 96 - add ace labels
    [aceA02-B_Cu.gbr, aceA02-B_Mask.gbr, aceA02-B_Paste.gbr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]
2025-05-18 issues 123, 125 - damper algorithm bugs
    [dsp_damper.cpp]
2025-05-18 issues 126, 127, 128
    [damper_settings.cpp, damper_status.cpp, hammer_settings.cpp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]
2025-05-31 issue 129 - add damper over Ethernet
    [dsp_damper.cpp, midiout.cpp, network.cpp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]
2025-05-31 issue 130 - processor burden
    [damper_status.cpp, hammer_status.cpp, src_damper.ino]
2025-11-29 Renamed to keep ArduinoIDE happy

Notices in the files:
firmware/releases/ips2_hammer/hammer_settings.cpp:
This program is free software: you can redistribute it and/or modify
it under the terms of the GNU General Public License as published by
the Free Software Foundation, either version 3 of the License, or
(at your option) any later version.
